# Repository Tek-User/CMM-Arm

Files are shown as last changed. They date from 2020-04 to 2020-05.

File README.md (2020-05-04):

# CMM-Arm

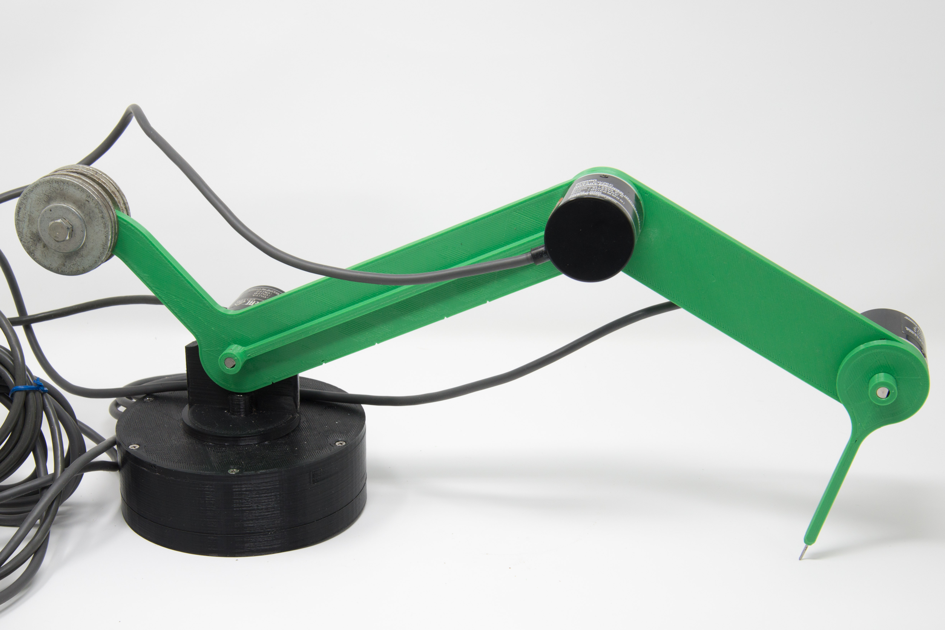
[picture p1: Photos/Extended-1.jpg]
<a href="https://github.com/Tek-User/CMM-Arm/blob/master/Photos/Extended-1.jpg"><br/></a>

Development of an accurate, inexpensive DIY CMM arm

(The photo above is of the first generation of the arm segments)

This project uses, as much as possible, 3D printed parts.  However, the rigidity of plastic arm sections, and the encoder pivots is sub-optimal, and hollow section aluminum arm segments with 3D printed connectors may be required for good accuracy.  At first, I had about +/-1mm accuracy even with careful measurements, avoiding twisting of any arm segments, and keeping the arm angles away from the extremes.  The newest version of the arm segments appears to have improved accuracy and reproducibility. Now the readings seem to average about 0.22mm variation, and no more than 0.34mm error. 

This has the potential to be a really good machine to obtain reasonably accurate X-Y-Z measurements.  However, real-world issues impede this goal.  If we can solve the following issues, then we have a great device!  I am looking for any input to solve these issues.

Issues: RIGID PARTS

I re-designed the shoulder and arm segments to have more stability.  They seem pretty good now.  I am sure there is room for improvement (e.g. cable management), but it seems like a reasonable design now.  As stated above, the newest design has reasonable accuracy, and maybe this is not as much of an issue now.

Issues: CALIBRATION

Regarding accuracy: to have good accuracy, you need a good calibration!  There are 3 factors that have an influence.  The calculation of the XYZ position is based on the length and position of each of 5 parts: the base, the shoulder, and each of the 3 arm segments.  This assumes there is no wobble of the axes in the encoder mechanism, and there is no bending/twisting of the arm segments!

1)  While we know the nominal lengths of the parts based on the CAD design, we do not know the actual length to 2 or 3 decimal places.  And the length is likely temperature sensitive, so if the temperature is different from the time that the exact length was determined, then the length estimates are likely wrong.

2)  We need to zero the position of the encoders.  The encoders measure relative rotation, so we need to know where they started.  I use a very crude method to zero the "elbow", and "wrist" encoders.  The "pivot" and shoulder encoders's starting positions are not critical to get good measurements of one XYZ position compared to another.  The relative positions are unaffected.  But if we need absolute position compared to the rest of the world, then we need an accurate zero of the pivot and shoulder encoders.

3)  We do not know the exact angle of joints.  I use encoders with as high a resolution as possible.  They are rated as "2000 p/r".  Quadrature encoders will have 4x as many quadrature transitions than that, so my encoders have an angular resolution of 1/8000 of a full circle.  With the arm fully extended it has a length of 200+150+100 = 450mm.  The pivot has a resolution of 1/8000 of the full circle (7.85e-4 radians). That means that the XYZ position resolution of the tip of the arm when fully extended is about 450 * 7.84e-4 (rule of thumb that the sine of a small angle equals the angle in radians).  This equals about 0.35mm.  And the inaccuracy propagates down the chain of arm sections and encoders, each amplifying the error of the previous ones.

So, we need to be able to zero the system regarding the exact length of each part of the system, and the exact angular position of them.  I THINK that a bunch of measurements of a standard item could be be used in simultaneous equations to solve for lengths and rotations of each part.  However, when I tried to grapple with that problem, my brain instantly started to fry.  I hope that someone out there can solve this conundrum.  I believe that a maybe an 8x8 matrix can be used to solve for starting points (zero positions and lengths).  But it is beyond me to solve it, or even verify that the general mathematical solution is correct!

With the new arm section designs, the accuracy seems acceptable with no calibration other than a simple zero-ing the elbow and wrist encoders.  I will investigate if it is feasible/useful to try to calibrate the arm section lengths beyond assuming the precise length is as designed.

AN ITEM LEFT TO DO:
Write a PC program (portable to other platforms) to record the ascii XYZ readings coming from the Arduino and save it to a file on the PC.  In addition it should show the point cloud in real-time as the data is being generated so we can be sure tht we have mapped all the required surface of the object.  Java or Python might be reasonable programming languages for an open source programming environment.  I have some experience with Java, and no experience with Python.  I have started the project in Jave.  It hsa been a while since I used it, and it is a bit of a learning curve to get off the ground.  I am using the NetBeans IDE for the project.

POST PROCESSING:
Right now I use an assemblage of freeware to take the point cloud and generate a mesh.  I use Meshlab for this.  But I find this cumbersome to work with in general, so I aso use MeshMixer and Blender to re-scuplt the mesh.  Once we get improved accuracy of the XYZ readings, then there will be much reduced need to massage the mesh!!!

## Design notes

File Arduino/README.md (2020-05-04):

This folder contains the arduino project for the 4-axis CMM arm.

I saw several other, somewhat similar projects with Arduino code.  However, it was a little hard to understand exactly what they were doing, and I decided to write the code entirely on my own.

The strategy, which I have nt seen in any of the other projects is to use interrupt-based recording of the encoder positions.  I use pin change interrupts for all the encoders.  I try to split the encoders across all the available ports in order to reduce the interrupt processing for any single interrupt.

Certainly all the encoders could occupy a single port, and it may actually be faster overall to do so.  I have not compared overhead processing of the interrupt for 1, 2 and more encoders on a single port versus spread over multipe ports.

I believe the use of interrupts is superior to the use of a timer, which could miss encoder transistions if they occur too quickly, and also occupies a lot of CPU time polling the encoder pins even when they are not changing.

The software also allows for single point reading, as well as high speed continuous point reading.  I believe the maximum bandwidth is maybe up to 70 readings/second, but this seems to be excessively fast.  The software uses a timer to pace the readings (not a timer to poll the encoders).  Between readings, the encoder counters may well get updated many times.

Other projects use a "Kinematic Chain" calculation to determine the XYZ position of the tip of the arm.  These calculations are a more general solution to the calculation of the position, but unnecessarily complex for this project.  All segments are co-planar, and ideally have unchanging length and no out-of-plane rotation.  So, a simple triginometric calculation will suffice.  The kinematic chain calculation likely uses an order of magnitude more transcendal calculations.  On a system with no math coprocesor, like an Arduino, these are very time consuming calculations.

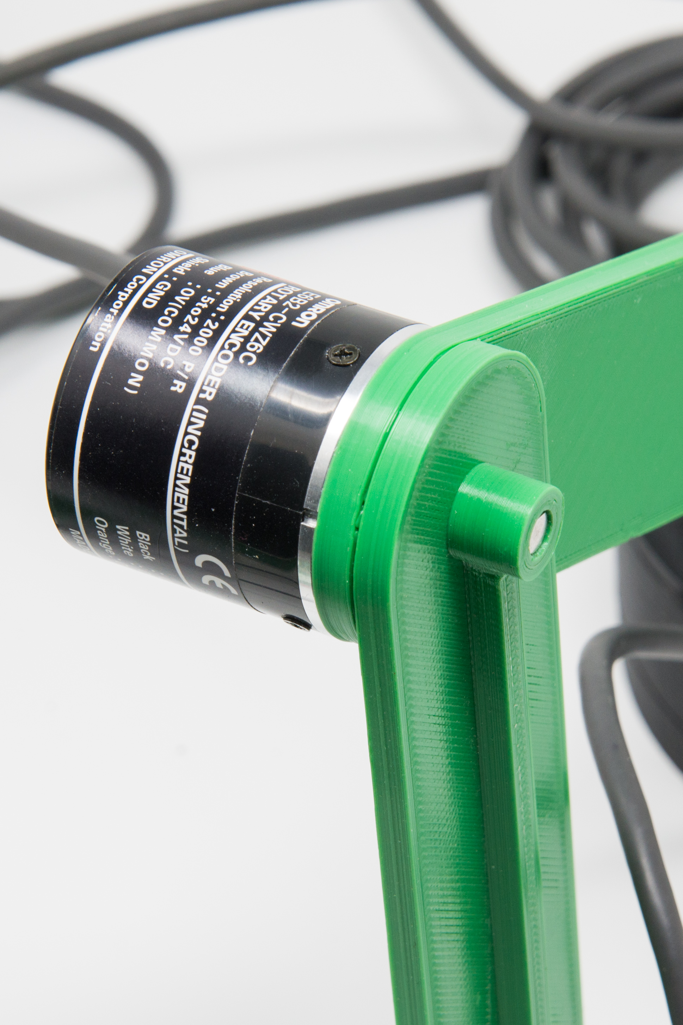
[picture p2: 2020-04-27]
Photos/Elbow-.jpg

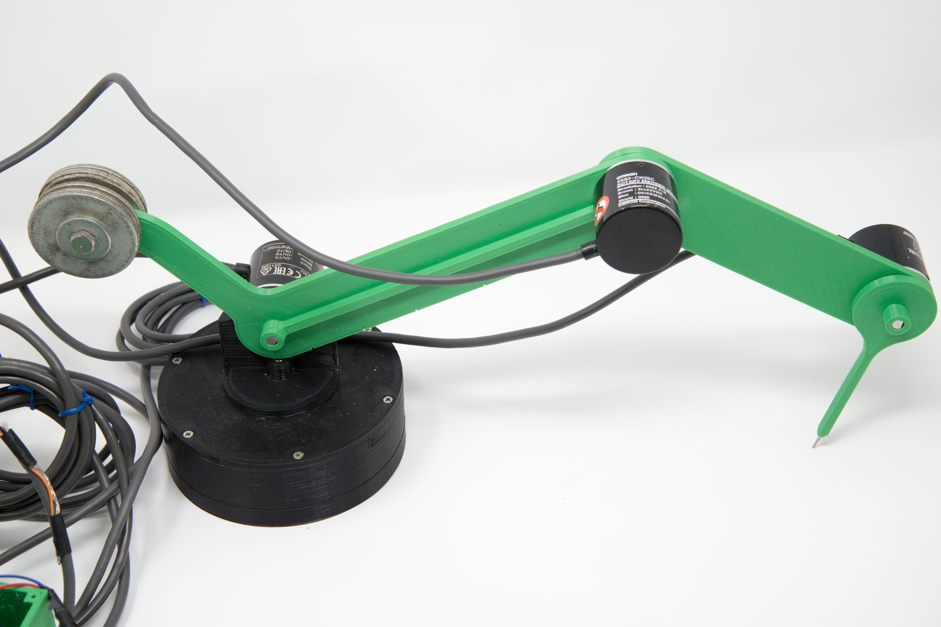
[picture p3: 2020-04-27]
Photos/Extended-2.jpg

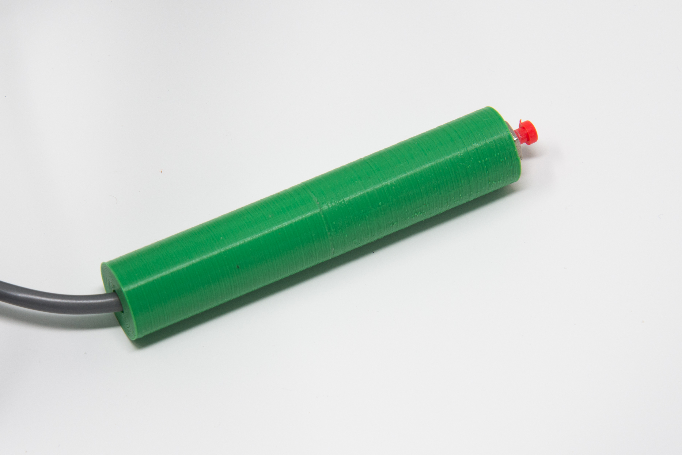
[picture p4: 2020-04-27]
Photos/Handpiece.jpg

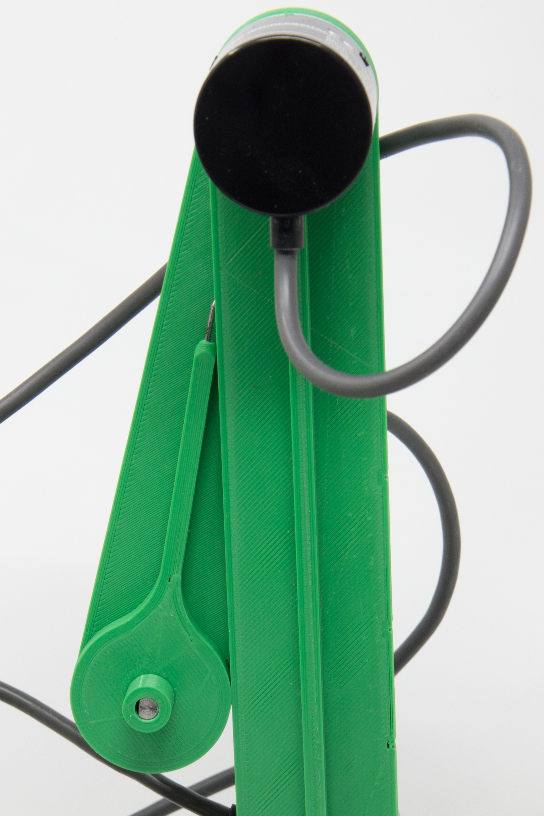
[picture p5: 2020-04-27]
Photos/Parked-Pos-2-CloseUp.jpg

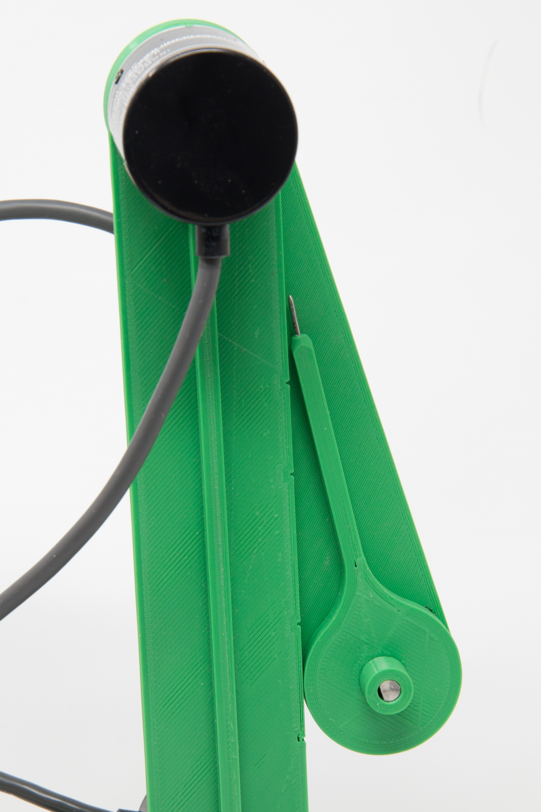
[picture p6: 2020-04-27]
Photos/Parked-Pos-1-CloseUp.jpg

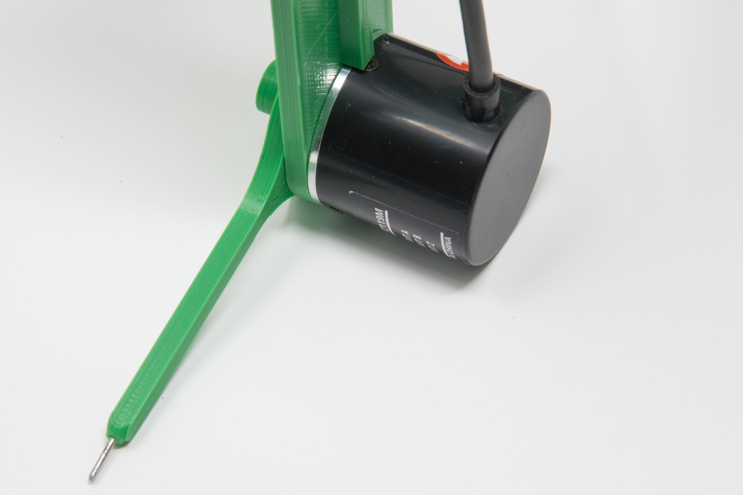
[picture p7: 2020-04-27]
Photos/Wrist-1.jpg

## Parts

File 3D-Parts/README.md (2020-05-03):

This folder contains all the 3D printable parts. 

I have revised, yet again, the arm segments to improve rigidity of the arm over its length as well as the stability of the joints.  The rigidity was improved with a larger cross section area, and improved shape (as round as feasible).  Joint stability was improved by increasing the diameter of the round areas facing each other.  It went from 40mm to 60mm, and this allows there to be good support all around the seating areas of the encoders.  This is MUCH more stable overall than the original design, though it does weigh more too.  As we get further out the arm, we have lower loads, and therefore the sections can be thinner.

The third arm section, the "pointer" is in two versions.  The pretty, curved one is hard to hold, my fingers slip on the curves.  The second one is more like a pencil and easier to hold, though it is less rigid.  Both versions have a hole in the tip to accept a small wire brad nail.  I used a nail that is 0.069" in diameter (1.75mm).  It should have exactly 10mm protrusion beyond the plastic pointer tip for both versions.

The base is designed to be toroidal.  The inside of the torus is intended to hold a heavy powder or granular substance.  I used lead shot because I had it on hand and it is quite heavy.  Filled, the base weighs about 2.3kg (11.3g/cc).  If filled with sand, it would likely weigh only about 0.3kg (1.6g/cc), which is probably not enough.  Fine aluminum granules would be heavier than sand (2.7g/cc or more depending on the alloy).  Brass has a density of 8.53g/cc, and steel is about 8.05g/cc.  Probably the cheapest per kilo is lead, and it is NOT cheap!  When I bought that lead a couple of decades ago, I do not recall it being particularly expensive at all!  Upon further checking, it appears that you can get "reclaimed lead shot" on the internet quite cheaply (per kilo), but I did not see just 2-3kg units available.  There are sources for scuba diving ballast lead shot in 1 and 5 pound units.

The base's toroidal allows the encoder to be serviced wouthout emptying the base of its contents.

Where possible a hole is provided for drilling/tapping for a set screw to hole the encoder axle securely.  The  hole to accept the encoder axle is tuned to the "squish" of my printer.  The axle is nominally 6mm diameter.  I bore out the holes in the arm sections with a 6mm drill to achieve a finger-tight friction fit.  The holes for the set screws fit 3mm stainless screws without formall drilling and tapping.

One issue that is not addressed in these arm section designs is cable management.  One option would be the placement of a central tubular passage in the first and second "thick" arm sections.  Another option applicable to all arm section designs is an additional built-up lug to hold a zip-tie.

Section 1 of the arm has a hooked projection with a 1/4" hole.  This is to attach 2" diameter heavy washers using a 1/4" bolt and nut.  My setup uses about 296 grams (maybe more with the larger cross section design) to provide a fairly neutral weight on the pointer tip.

I use six washers which have the following specifications.  OD: 2", ID: 0.812", thickness about 0.125"  Mine total to 0.825" thick.  I also use two 1" OD, ~0.25" ID, 0.062" thick washers, 1x bolt; 1.5" length, 1/4-20 and matching nut.

Ideally the thick washers would have 1/4" ID, but then you would need fewer washers, maybe about a total of 0.75" thickness of washers.  Mcmaster-Carr has "Oversize Washers" like mine at $8.90 for 10 pieces.  They also have "Metric Oversize Washers" at OD: 540mm, ID:17mm, thickness: 2.7-3.3mm  At a cost of $13.16 for 25 pieces.

McMaster also has oversize washers with OD: 2", ID: 1/4" Thickness 0.042-0.051.  You would need about 17-18 of these, or a little fewer due to smaller ID.  The cost these is $6.11 for 25 pieces and you would use about 18 or fewer of them.  This is likely the cheapest option and it gives the best ability to dial-in the required amount of counter weight.

The top of the base is held by twelve #4 x 5/8" sheet metal screws.  I found that only 6 around the perimeter still allowed the lid to flex a little with off-center torques to the encoder axle.  It is substantially more rigid with the added inner ring of 6 screws.

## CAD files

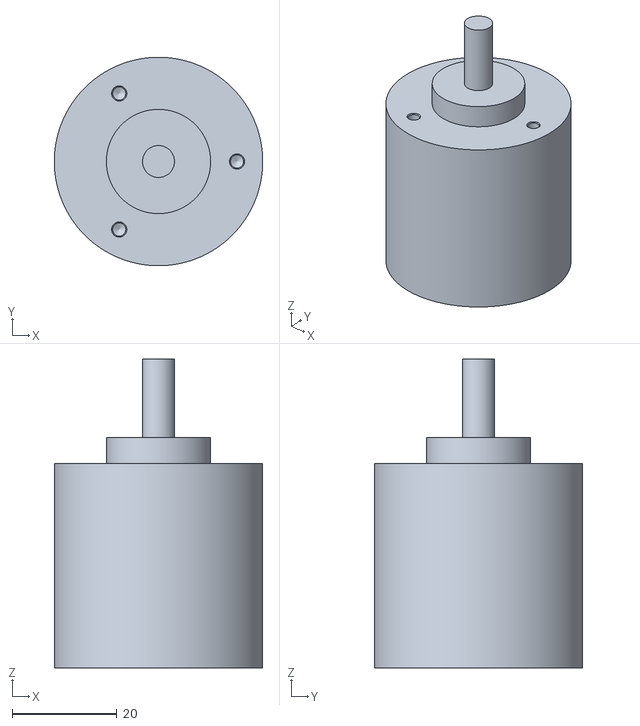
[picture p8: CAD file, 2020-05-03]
3D-Parts/Dummy-Encoder.stl
39.8 x 39.8 x 59.0

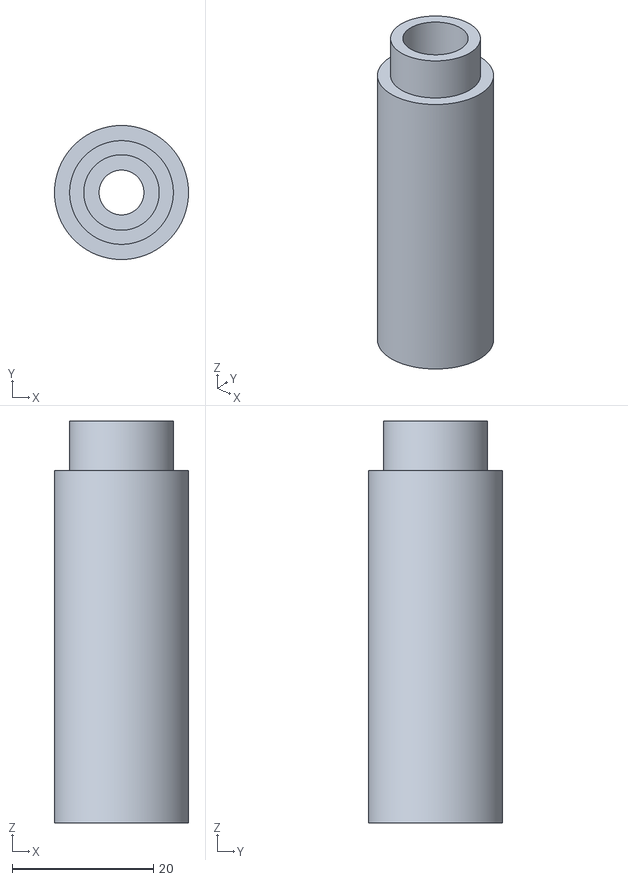
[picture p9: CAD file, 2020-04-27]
3D-Parts/Handpiece-A.stl
19.0 x 19.0 x 57.0

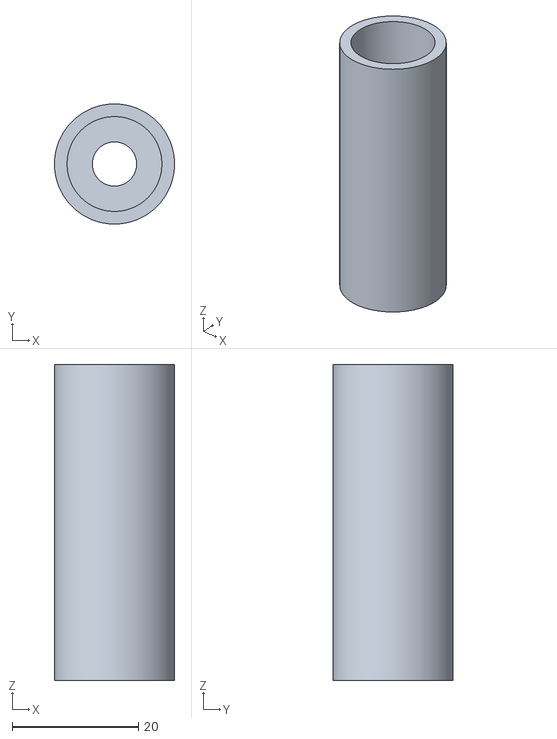
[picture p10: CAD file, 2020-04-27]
3D-Parts/Handpiece-B.stl
19.0 x 19.0 x 50.0

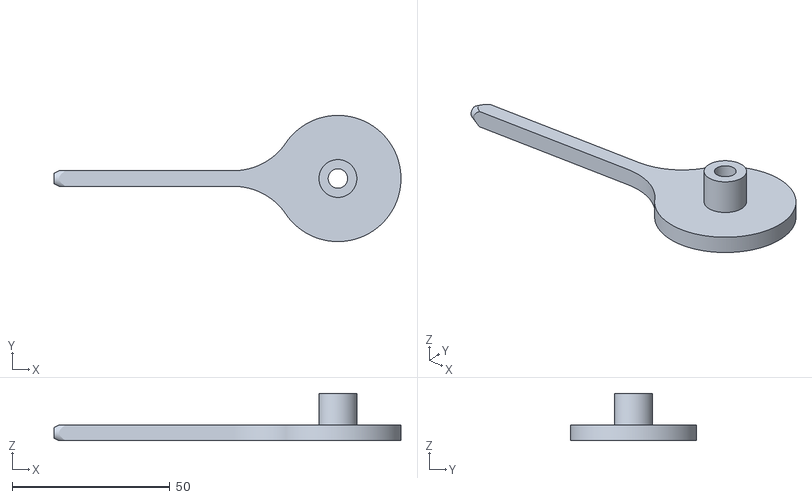
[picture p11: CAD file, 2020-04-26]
3D-Parts/Arm-Section-3-Type-2.STL
110.0 x 40.0 x 15.0

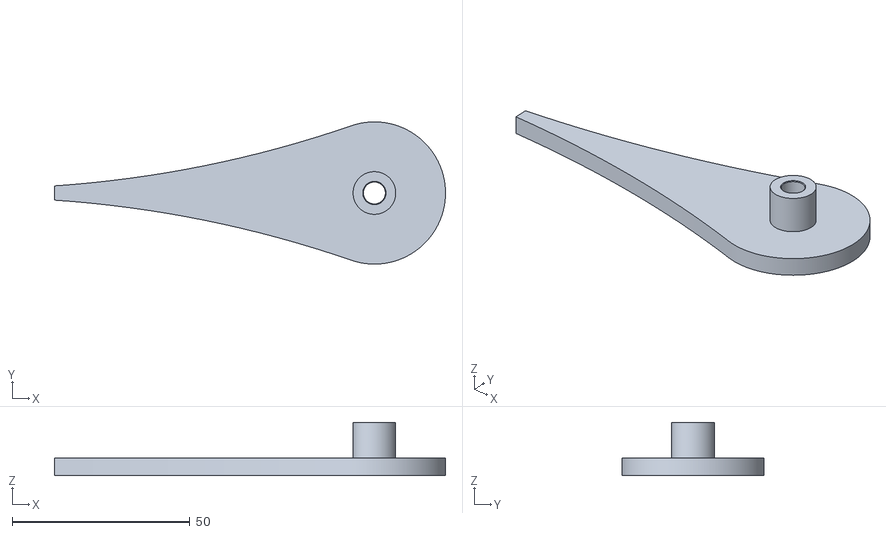
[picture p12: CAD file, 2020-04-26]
3D-Parts/Arm-Section-3-Type-1.STL
110.0 x 40.0 x 15.0

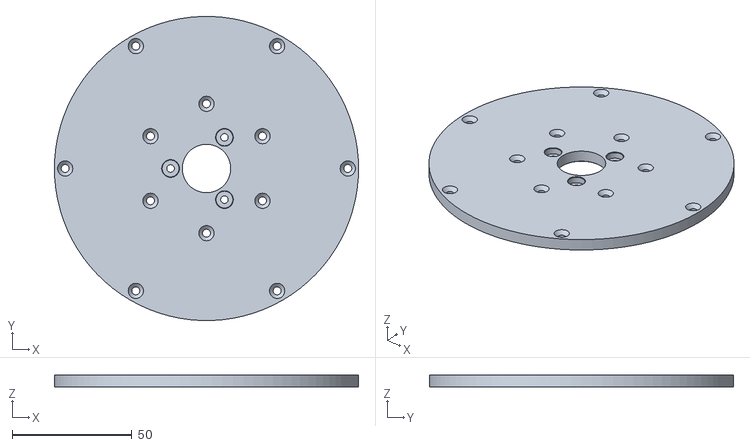
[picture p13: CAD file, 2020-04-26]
3D-Parts/Arm-Base-Top.stl
127.0 x 126.9 x 5.00

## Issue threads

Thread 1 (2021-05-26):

Calibration idea

tealvince, 2021-05-26:
Very cool project.  I might be able to help with the calibration.  My M.E. masters project many years ago involved brute force calculation the position of joints in a robotic arm from the data of two video cameras.  I think the approach would work here.  When I get a chance, I'll take a deeper look to see if I can make a unit for testing.

Tek-User, 2021-05-26:
That is really good to hear!   I found that assuming that the arm lengths were as nominally specified have better results of measurements that iteratively trying to solve multiple simultaneous equations for X,y,z position given length and angle of each arm and sensor.

Let me know how it works out!  I will post the solution.

One concern I have with using several video cameras is that if you have that equipment then you might be able to use it directly to determine the 3D point cloud of the surfaces!

-Tony

Sent from my 1837 Babbage Analytical Engine

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

Tek-User, 2021-05-26:
 That is really good to hear!   I found that assuming that the arm lengths were as nominally specified have better results of measurements that iteratively trying to solve multiple simultaneous equations for X,y,z position given length and angle of each arm and sensor.

Let me know how it works out!  I will post the solution.

One concern I have with using several video cameras is that if you have that equipment then you might be able to use it directly to determine the 3D point cloud of the surfaces!

-Tony

Sent from my 1837 Babbage Analytical Engine

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

maximator25, 2024-10-21:
Colleagues, if u still have an interest, I can make mech parts,please write to the mail,hatber2@gmail.com
